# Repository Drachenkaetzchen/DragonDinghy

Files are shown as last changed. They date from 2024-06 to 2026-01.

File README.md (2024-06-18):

DragonDinghy is a small expansion board for Klipper. Your main ship is damaged and lost some of it's functionality? DragonDinghy has you covered. 4 fan Ports (2x GND-switched with tacho, 2x 4-wire fan ports), 4x Neopixel outputs, 9 thermistor inputs, 2x I²C ports, 12V 2A and 5V 2A voltage regulator onboard. Can be operated via USB or CAN

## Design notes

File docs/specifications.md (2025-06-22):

# Specifications

## Main Features

* 9 Thermistor Inputs
    * 5 Inputs best suited for 100k NTCs, like Generic 3950 or ATC Semitec
    * 4 Inputs best suited for PT1000
* 4 Fan Outputs
    * 2 GND-switched PWM fan ports with optional tachometer support, 1 A per port
    * 2 4-pin Fan Ports, 2 A maximum per port
    * Each fan output supports 5V, 12V and 24V fans
* 4 RGB Outputs (compatible with WS2812B, SK6812 and Adafruit Neopixel)
    * Integrated diagnostic SK6812 RGB LED  
    * up to 2A (shared with other 5V devices and across all 4 ports) 
* 2 I²C ports
* Integrated 12V 2A and 5V 2A step-down converters
* Usage via CAN or USB (or...use it as an USB to CAN bridge?)
* Raspberry Pi compatible mounting pattern
* Extensive Quality-of-Life Features
    * All ports are labeled on the board with the pinout and the respective pin for Klipper
    * Klipper `menuconfig` settings are printed on the board
    * Diagnostic LEDs for fan ports, DFU mode and power supply status
* Protection Features
    * Reverse Polarity Protection on the main input
    * Thermistor inputs withstand accidental short to 24V

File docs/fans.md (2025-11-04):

# Fans

This section explains how to figure out what fan you have, and where to connect it.

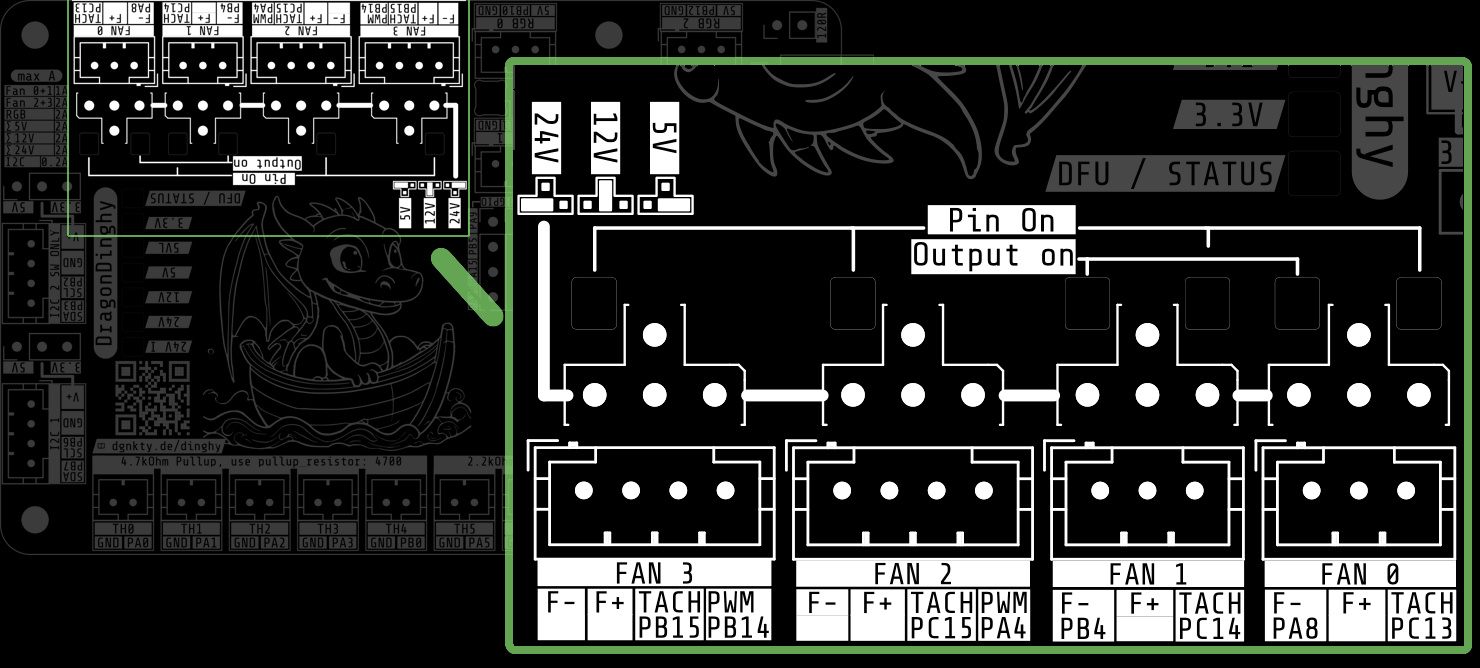
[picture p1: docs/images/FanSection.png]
Fan Section Overview


## Before connecting the fan

Prior connecting, ensure that the fan's maximum current is below the current of 1A (Fan 0/1) or 2A (Fan 2/3).

!!! note

    Please make sure that your fans don't have positive and negative shorted. This can happen easily during installation
    of the toolhead, and happens often behind the fan's label. Therefore, it is good practice to measure continuity
    between the positive and negative fan wires prior powering the printer on.

    While there is some protection of the fan ports, the control element (mosfet) of Fans 0 and 1 can easily blow
    before the protection fuse kicks in.

## Choosing the fan voltage

Use a jumper to select the voltage as indicated below.

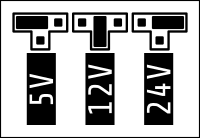
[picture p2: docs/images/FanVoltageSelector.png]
Fan Voltage Jumper


## 2-Wire Fans

Those are the most common type of fans in the 3D printer world. Their speed can only be controlled by rapidly turning
connecting and disconnecting either the positive or negative wire. DragonDinghy, like most other 3D printer boards,
switches these fans on the negative side.

You can connect these fans to the 3 pin fan headers (Fan 0 and Fan 1):

| Wire Color (typical) | Fan 0 | Fan 1 |
|---|---|---|
| Black | F- (PA8) | F- (PB4) |
| Red | F+ | F+ |

The third connector (TACH) is not used in this scenario.

Example Klipper Section:

```
# These are the example configurations for 2-wire fans on Fan 0 and Fan 1
[fan_generic dinghy_fan0]
pin: dinghy:PA8

[fan_generic dinghy_fan1]
pin: dinghy:PB4
```

!!! note 

    Genuine Sunon -A99 series are notoriously hard to control, often they only spin if the speed is set to 100%, and
    turn off or jitter at 99% or below. People have reported success by adjusting Klipper's `cycle_time` parameter,
    but it is by no means guaranteed that these types of fans can be controlled properly.

## 3-Wire Fans

These fans come with a 3rd wire. Most often, the function of those wires is either tachometer or PWM control. You need
to consult your fan's data sheet/seller page to figure out which function that 3rd wire has.

### 3-Wire Fans with Tachometer
For 3-wire fans with tachometers, you can use Fan 0 and Fan 1: 

| Wire Color (typical) | Fan 0 | Fan 1 |
|---|---|---|
| Black | F- (PA8) | F- (PB4) |
| Red | F+ | F+ |
| Blue (Delta), White (Orion), Yellow (GdsTime) | TACH (PC13) | TACH (PC14) |

!!! note

    A diode is already built-in on DragonDinghy, so there is no need to worry about
    the fan spinning or jittering when it's supposed to be off.

Example Klipper Section:

``` { .ini .copy }
# These are the example configurations for Fan 0 and Fan 1
[fan_generic dinghy_fan0]
pin: dinghy:PA8
tachometer_pin: dinghy:PC13

# The following 2 lines are optional, please read the note below
# tachometer_ppr: 2
# tachometer_poll_interval: 0.0009

[fan_generic dinghy_fan1]
pin: dinghy:PB4
tachometer_pin: dinghy:PC14

# The following 2 lines are optional, please read the note below
# tachometer_ppr: 2  
# tachometer_poll_interval: 0.0009
```

!!! note

    `tachometer_ppr` specifies how many impulses per one full fan rotation the fan outputs. That is almost always 2, if
    you have set your `tachometer_poll_interval` correctly, check the fan's datasheet if it uses a different value.

    `tachometer_poll_interval` specifies how often Klipper reads the tachometer pin. The value must be lower than
    `30/(tachometer_ppr*rpm)`. For example, the Delta ASB02505SHA-AY6B requires a poll interval of `0.0009`. Don't use
    arbitarily small values, as this requires additional computational time on the MCUs and can lead to a
    `Timer too close` if improperly configured. 

### 3-Wire Fans with PWM
For 3-wire fans with pwm, you can use Fan 2 and Fan 3. The TACH connector position stays empty in this scenario.

| Wire Color (typical) | Fan 2 | Fan 3 |
|---|---|---|
| Black | F- | F- |
| Red | F+ | F+ |
| Yellow (Delta), Blue (GdsTime, Orion) | PWM (PA4) | PWM (PB14 ) |

Example Klipper Section:

``` { .ini .copy }
# These are the example configurations for Fan 0 and Fan 1
[fan_generic dinghy_fan2]
pin: dinghy:PA4

[fan_generic dinghy_fan3]
pin: dinghy:PB14
```

## 4-Wire Fans

These fans come with 4 wires. Almost always, the additional wires functions for PWM control and tachometer feedback.

These fans go to the Fan 2 and Fan 3 connectors:

| Wire Color (typical) | Fan 2 | Fan 3 |
|---|---|---|
| Black | F- | F- |
| Red | F+ | F+ |
| Blue (Delta), White (Orion), Yellow (GdsTime) | TACH (PC15) | TACH (PB15) |
| Yellow (Delta), Blue (GdsTime, Orion) | PWM (PA4) | PWM (PB14)  |

Example Klipper Section:

``` { .ini .copy }
# These are the example configurations for Fan 0 and Fan 1
[fan_generic dinghy_fan2]
pin: dinghy:PA4
tachometer_pin: dinghy:PC15

# The following 3 lines are optional, please read the note below
# cycle_time: 0.00004
# tachometer_ppr: 2
# tachometer_poll_interval: 0.0009

[fan_generic dinghy_fan3]
pin: dinghy:PB14
tachometer_pin: dinghy:PB15

# The following 3 lines are optional, please read the note below
# cycle_time: 0.00004
# tachometer_ppr: 2  
# tachometer_poll_interval: 0.0009
```

!!! note

    `tachometer_ppr` specifies how many impulses per one full fan rotation the fan outputs. That is almost always 2, if
    you have set your `tachometer_poll_interval` correctly, check the fan's datasheet if it uses a different value.

    `tachometer_poll_interval` specifies how often Klipper reads the tachometer pin. The value must be lower than
    `30/(tachometer_ppr*rpm)`. For example, the Delta ASB02505SHA-AY6B requires a poll interval of `0.0009`. Don't use
    arbitarily small values, as this requires additional computational time on the MCUs and can lead to a
    `Timer too close` if improperly configured.

    `cycle_time` specifies the PWM base frequency. Most PC and server fans expect a 25kHz signal, equalling to
    `cycle_time: 0.00004`

## Troubleshooting

### Fans not spinning

- Ensure that the polarity of the wires is correct.
- Check the voltage status LEDs, they should all be lit

- Check that the `Pin On` LED is lit when you activate the fan.
 
      - If it doesn't light up, you might have the pins set incorrectly. Consult the Klipper log to check that the pins are
        actually set to what you expect them to be set.

#### Fans 0 and 1

- Check that the `Output On` LED is lit when you activate the fan. If it doesn't light up:

      - Ensure the fan voltage jumper is set
      - Ensure the fan is actually connected
      - If the previous checks come back false, then the protection fuse might be blown. This only happens when a severe
        overload happened, for example a short circuit or attempting to run a fan which exceeds the current rating of 1A.
        This fuse is not user replaceable, as other components in that part of the circuit might have taken damage. 

### Fan spinning uncommanded

#### Fans 0 and 1

Check the LEDs of the fan port. If the `Pin On` LED is lit, then something has commanded the fan to spin. This is
typically a misconfiguration or macro on the Klipper side. If `Output On` LED is lit but `Pin On` is not, then the
output has experienced a brief overload (typically a short circuit), fast enough to damage the control element (mosfet)
but not triggering the protection fuse.

#### Fans 2 and 3

Most PWM fans start up at full power until Klipper has started and initialized the MCU board(s). To prevent this,
you can set initial pins in your `make menuconfig` section like so:

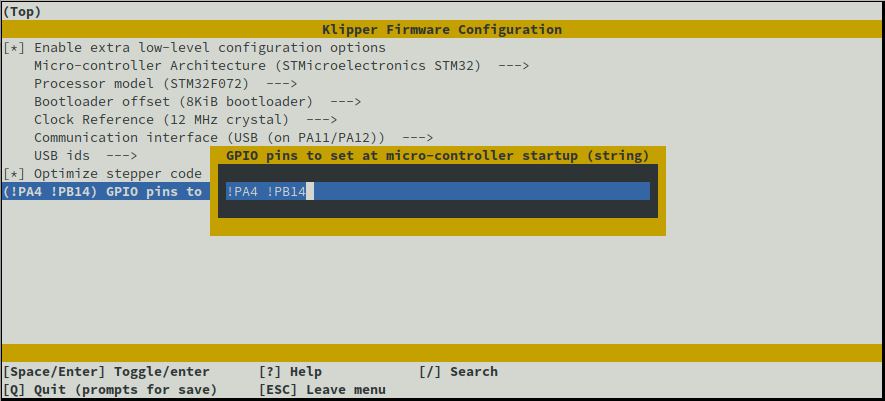
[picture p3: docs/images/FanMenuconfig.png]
Board Diagram


### PWM fans not properly controllable

Many PWM fans designed for use within computers or servers (GdsTime GDP4028, Noctua Fans, almost all PC fans) expact
a 25kHz signal. To implement this, add the following line to your PWM fan section: 

```ini
cycle_time: 0.00004
```

## Appendix
### Typical Fan Wire Colors

This table was written with the most common 3D printer fan models/types in mind. Note that sometimes manufacturers vary
the wire colors by fan model or target audience, so you might want to double-check the fan's data sheet for the most
accurate information.

| Function | Colors |
|---|---|
| Red | Positive supply voltage |
| Black | Negative / GND |
| Tachometer | Blue (Delta), White (Orion), Yellow (GdsTime) |
| PWM Speed Control | Yellow (Delta), Blue (GdsTime, Orion) |
| Alarm | Yellow (Orion) |

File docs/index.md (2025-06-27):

# DragonDinghy

DragonDinghy is a small expansion board for use with [Klipper](https://klipper3d.org).

!!! danger "Work in progress"

    This documentation is a work in progress. Please check back regularly!

    Sadly, it is very warm here, so documentation updates might be delayed. In case of urgent assistance,
    you can always drop an E-Mail to info (at) replimat dot eu with your questions or ask in the #replimat channel
    on the Voron discord.

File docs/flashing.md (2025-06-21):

# Introduction

To make your new board work, you need to put the MCU firmware onto the board. Depending on your scenario, you should use
the excellent guides from Esoterical:

[Esoterical's CAN Bus Guide](https://canbus.esoterical.online/){ .md-button }
[Esoterical's USB Guide](https://usb.esoterical.online/){ .md-button }

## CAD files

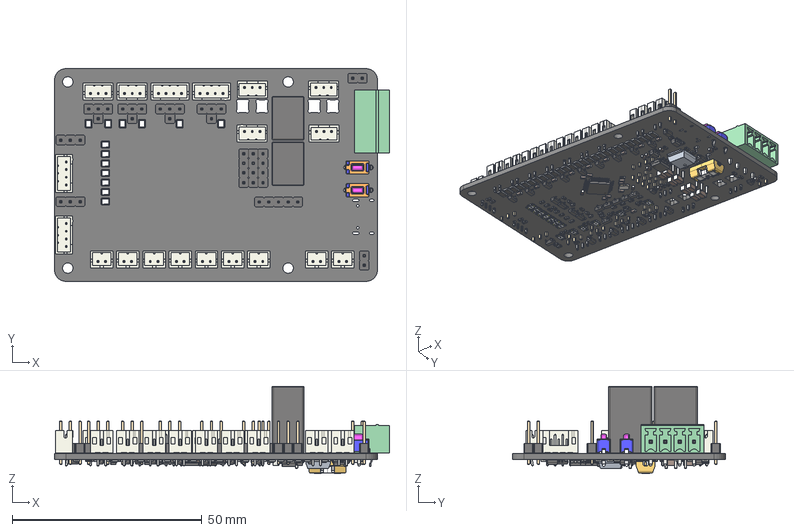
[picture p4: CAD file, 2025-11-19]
STEP/DragonDinghy.step
88.2 x 56.0 x 23.0 mm
SKHLAD x 2
PinHeader_1x05_P2.54mm_Vertical
JST_PH_B4B-PH-K_1x04_P2.00mm_Vertical x 4
JST_PH_B3B-PH-K_1x03_P2.00mm_Vertical x 6
PinHeader_1x03_P2.54mm_Vertical x 6
PinHeader_1x01_P2.54mm_Vertical x 4
JST_PH_B2B-PH-K_1x02_P2.00mm_Vertical x 9
PinHeader_1x04_P2.54mm_Vertical x 3
PinHeader_1x02_P2.54mm_Vertical x 2
PhoenixContact_MC_1,5_4-G-3.81_1x04_P3.81mm_Horizontal
Converter_DCDC_RECOM_R-78B-2.0_THT x 2
R_0603_1608Metric x 45
D_SOD-123 x 6
C_0603_1608Metric x 26
Fuse_0603_1608Metric x 5
R_1206_3216Metric x 27
DragonDinghy 1.49.1
LED-SMD_L3.2-W1.6-RD-EH_WHITE x 13
SOT-23 x 20
C_1206_3216Metric x 8
D_SOD-523 x 4
SOT-23-6
Komponente1
Komponente2
Komponente3
Komponente4
SOIC-8_3.9x4.9mm_P1.27mm
SOT-23-5
SOT-363_SC-70-6 x 3
Crystal_SMD_3225-4Pin_3.2x2.5mm
LQFP-48_7x7mm_P0.5mm
DragonDinghy_PCB

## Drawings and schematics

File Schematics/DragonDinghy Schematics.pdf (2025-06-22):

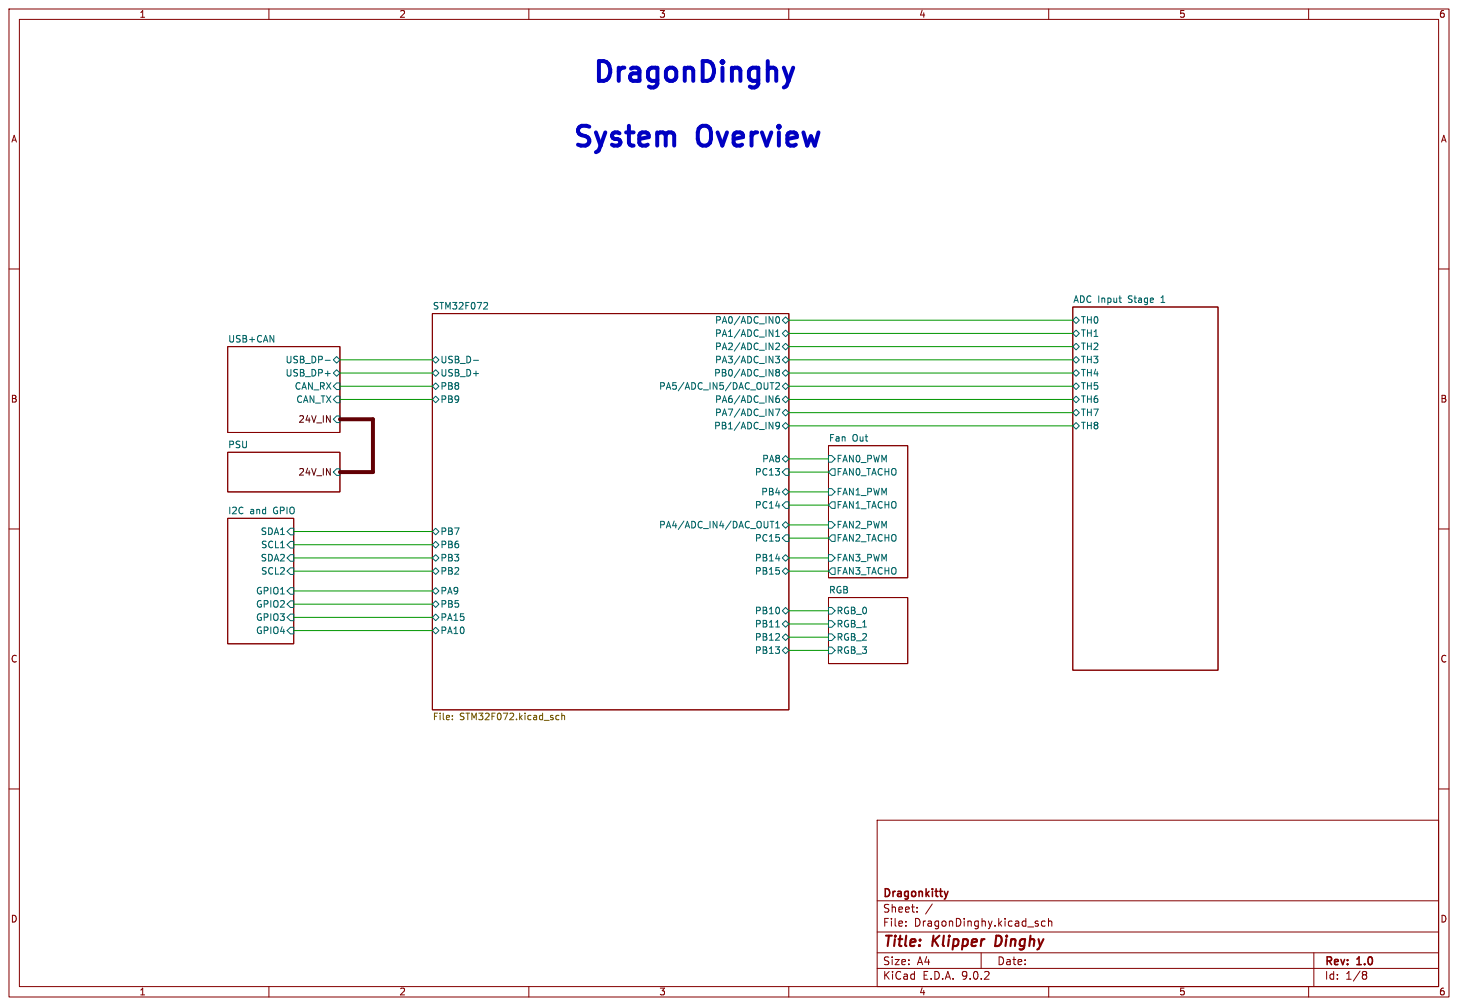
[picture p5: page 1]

File: DragonDinghy.kicad_sch Sheet: / Dragonkitty

Id: 1/8 Title: Klipper Dinghy

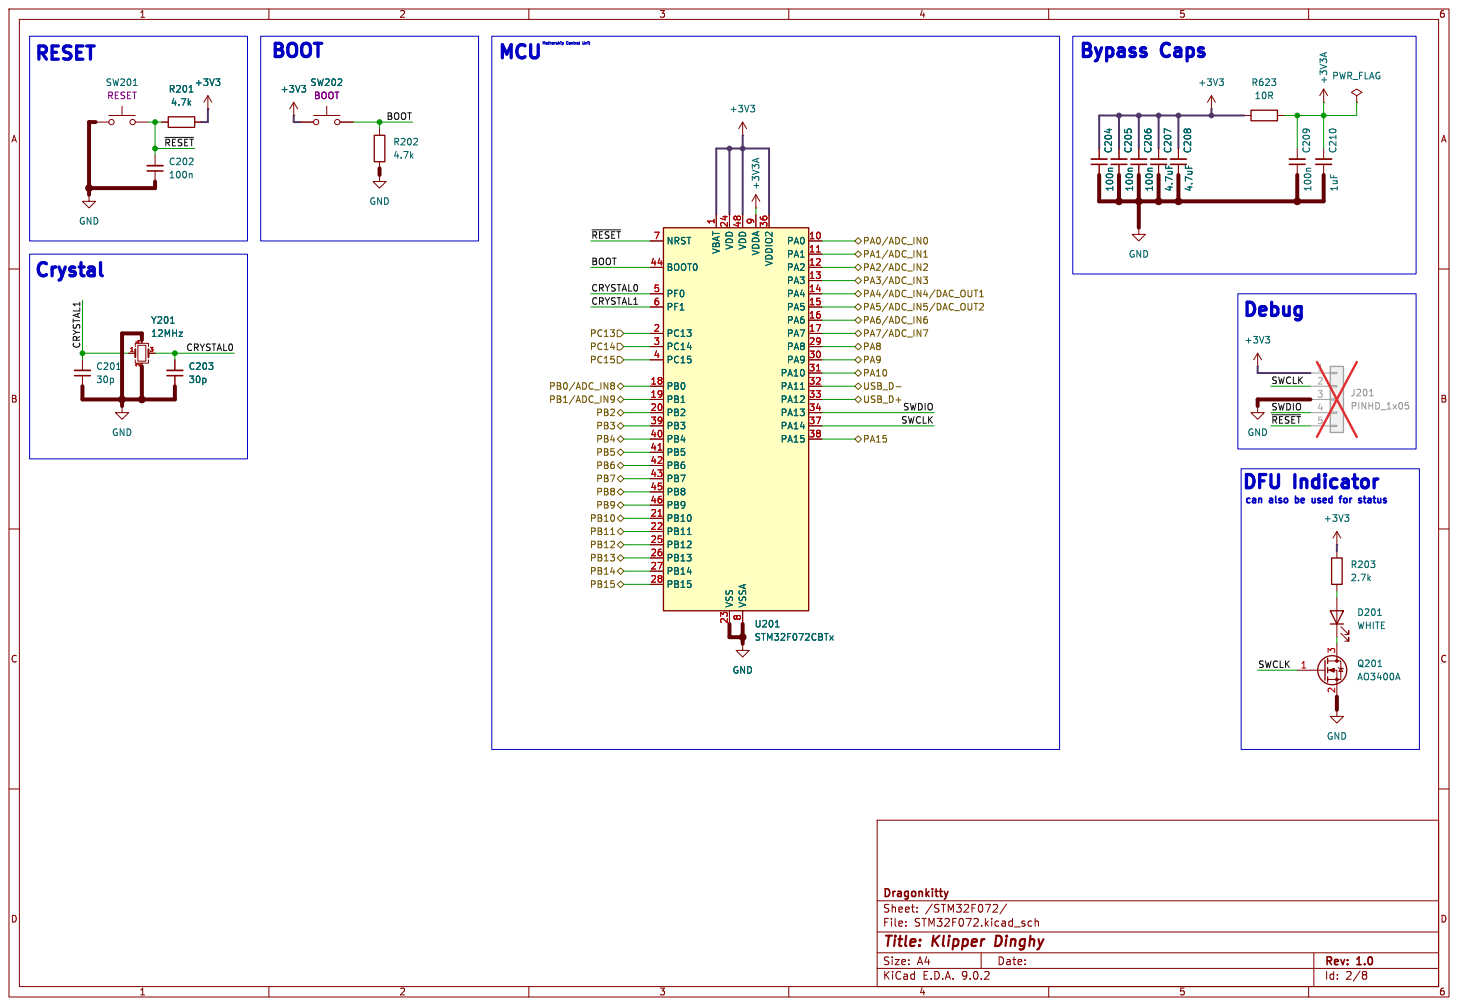
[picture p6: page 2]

can also be used for status RESET

1 VDD 24 VSS 23 VDD 48 VSSA

Id: 2/8 Title: Klipper Dinghy

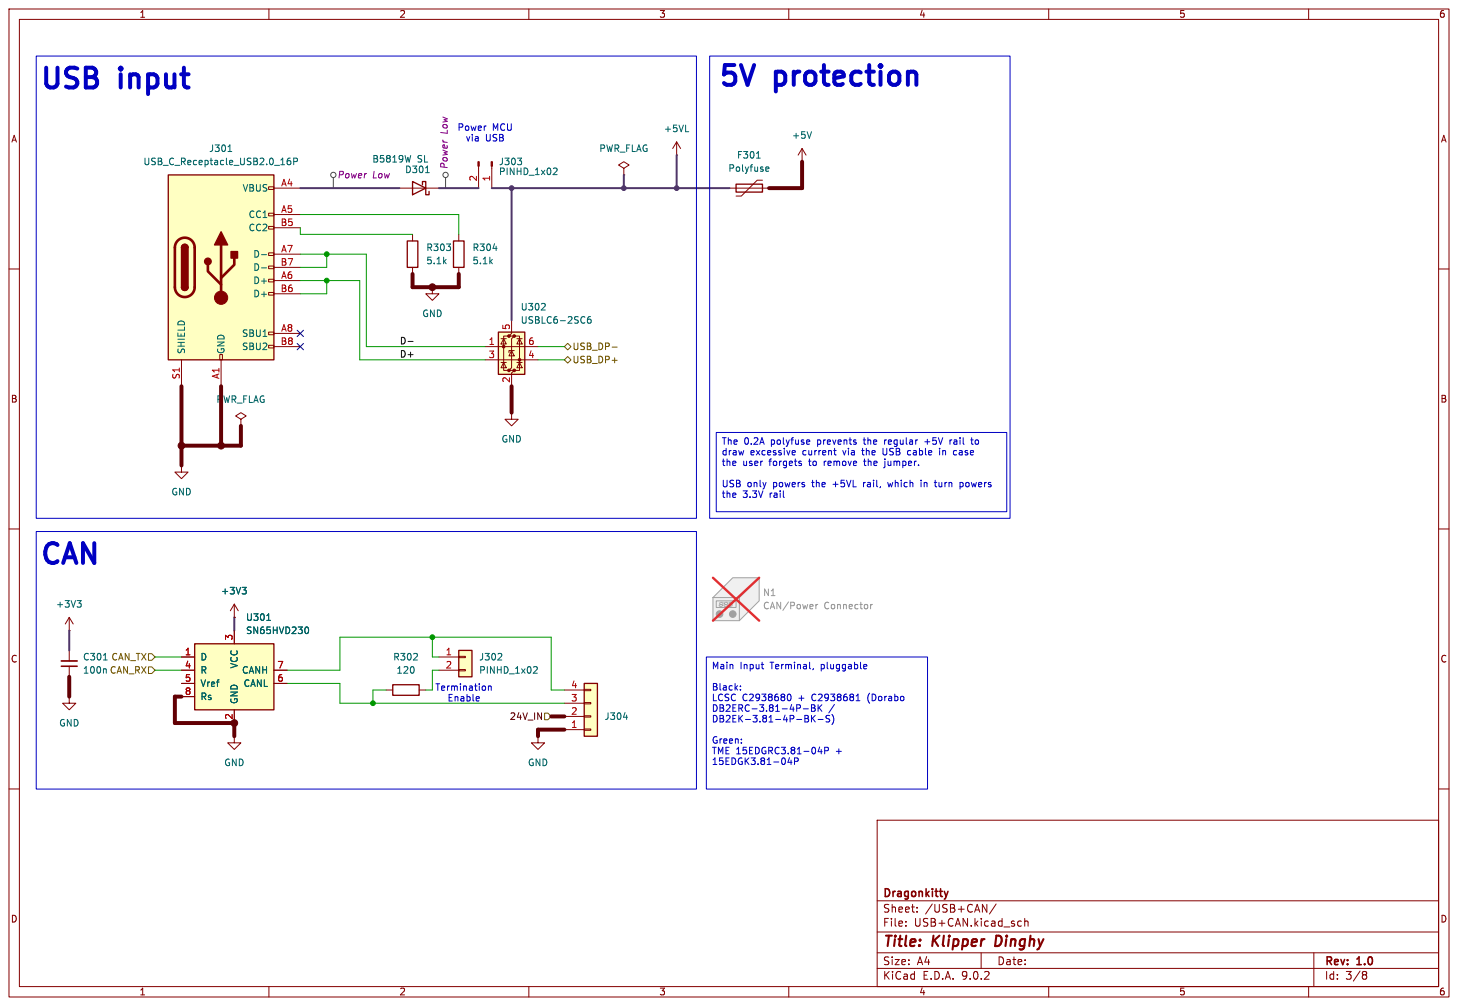
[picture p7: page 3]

draw excessive current via the USB cable in case
the user forgets to remove the jumper. USB only powers the +5VL rail, which in turn powers

File: USB+CAN.kicad_sch Sheet: /USB+CAN/ Dragonkitty GND

Id: 3/8 Title: Klipper Dinghy

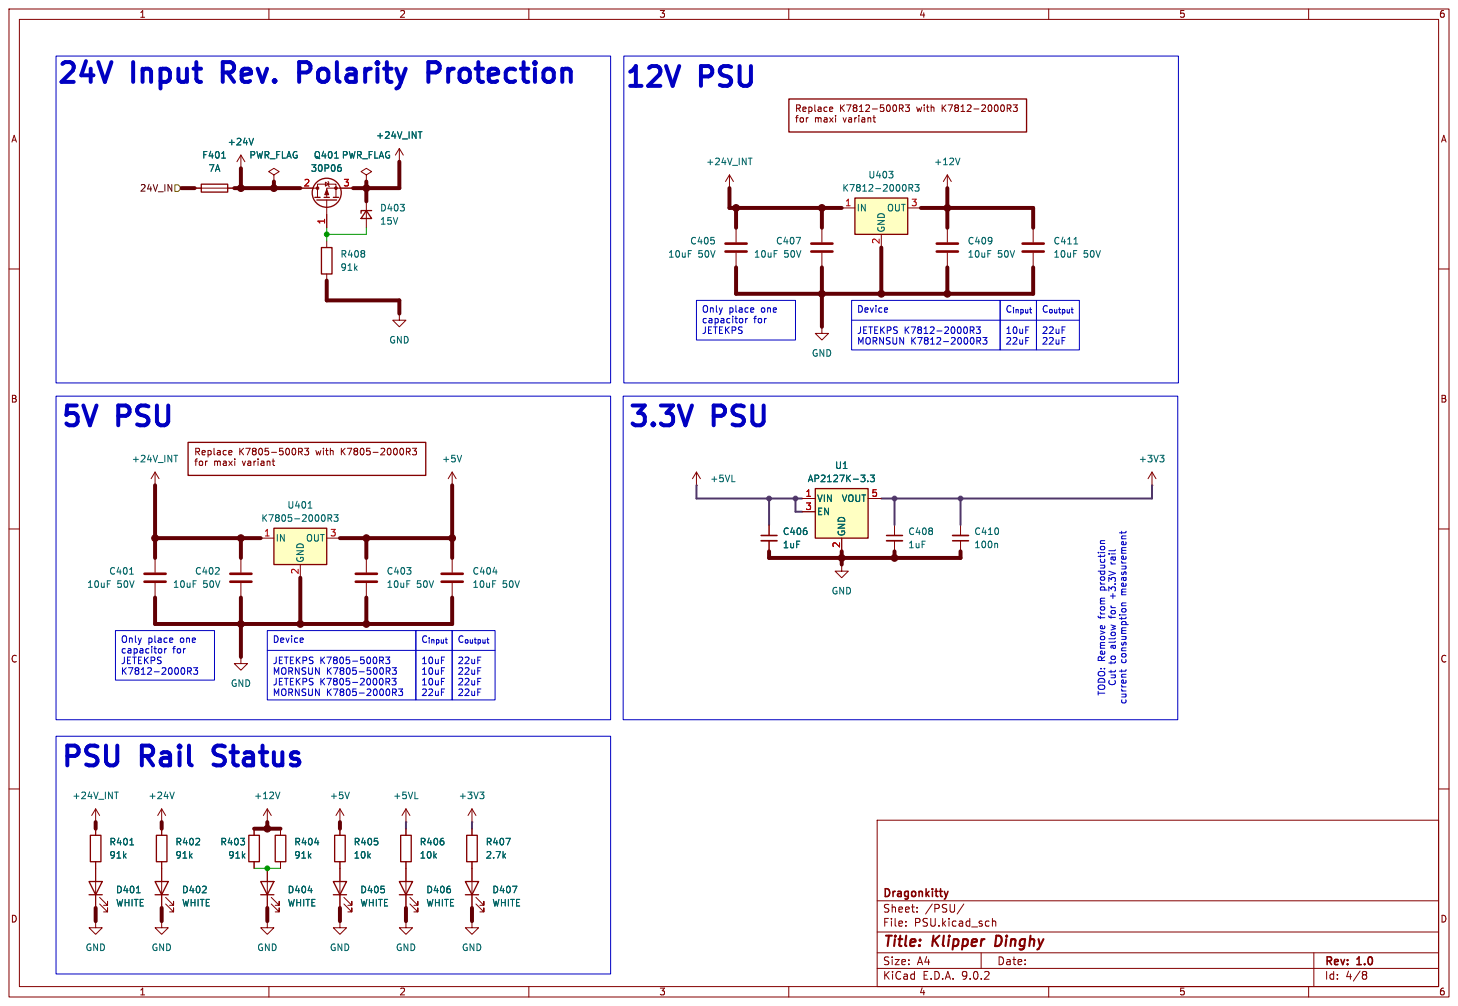
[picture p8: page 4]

24V Input Rev. Polarity Protection

for maxi variant Only place one

+24V_INT C401

Id: 4/8 Title: Klipper Dinghy

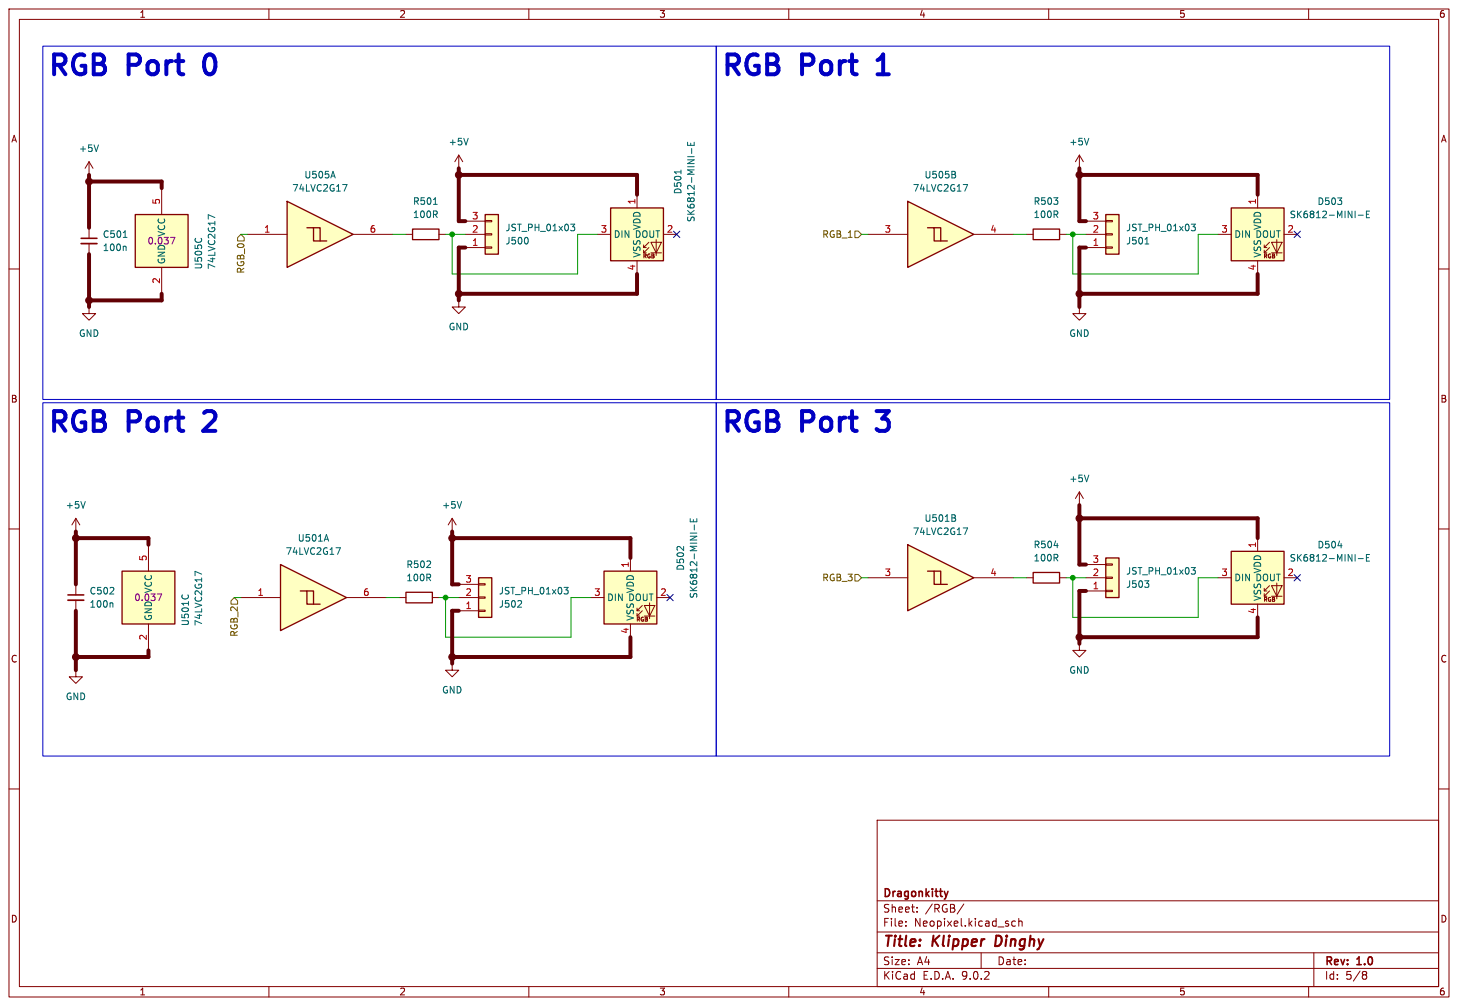
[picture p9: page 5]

2 U501C 74LVC2G17 0.037 RGB_3 RGB_0 RGB_2 RGB_1 RGB Port 2 RGB Port 3

File: Neopixel.kicad_sch Sheet: /RGB/ Dragonkitty

Id: 5/8 Title: Klipper Dinghy

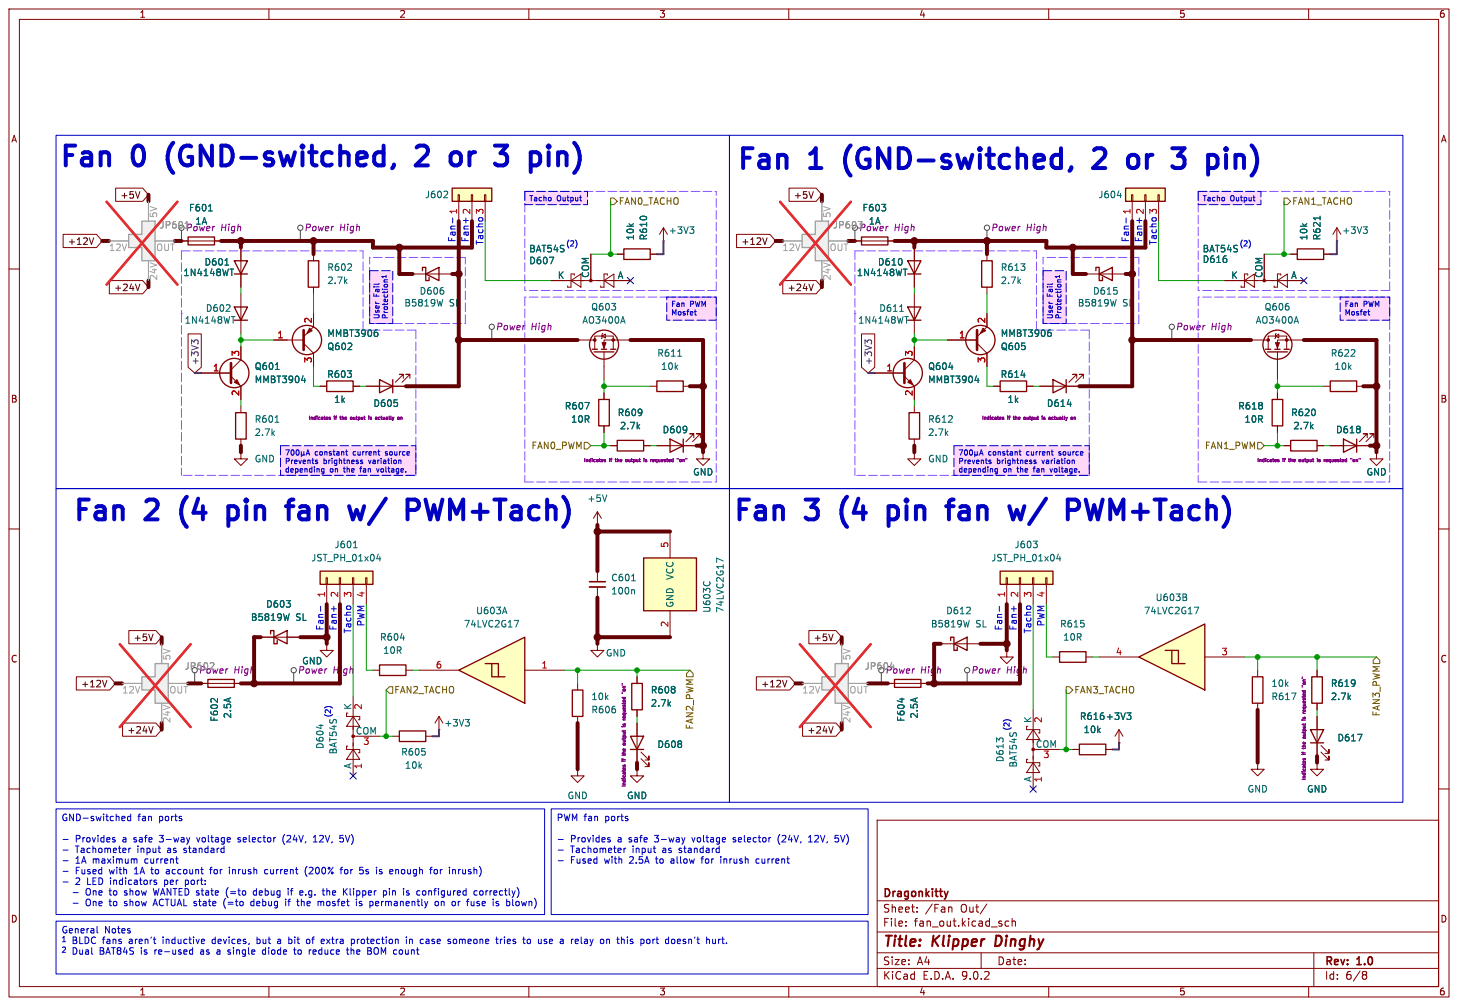
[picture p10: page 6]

Fan 3 (4 pin fan w/ PWM+Tach) Tacho PWMD603 B5819W SLGND F602 2.5A

Fan 2 (4 pin fan w/ PWM+Tach)

2.7k GND
D608 Indicates if the output is requested "on" GND

- Fused with 2.5A to allow for inrush current

File: fan_out.kicad_sch Sheet: /Fan Out/ Dragonkitty

Id: 6/8 Title: Klipper Dinghy

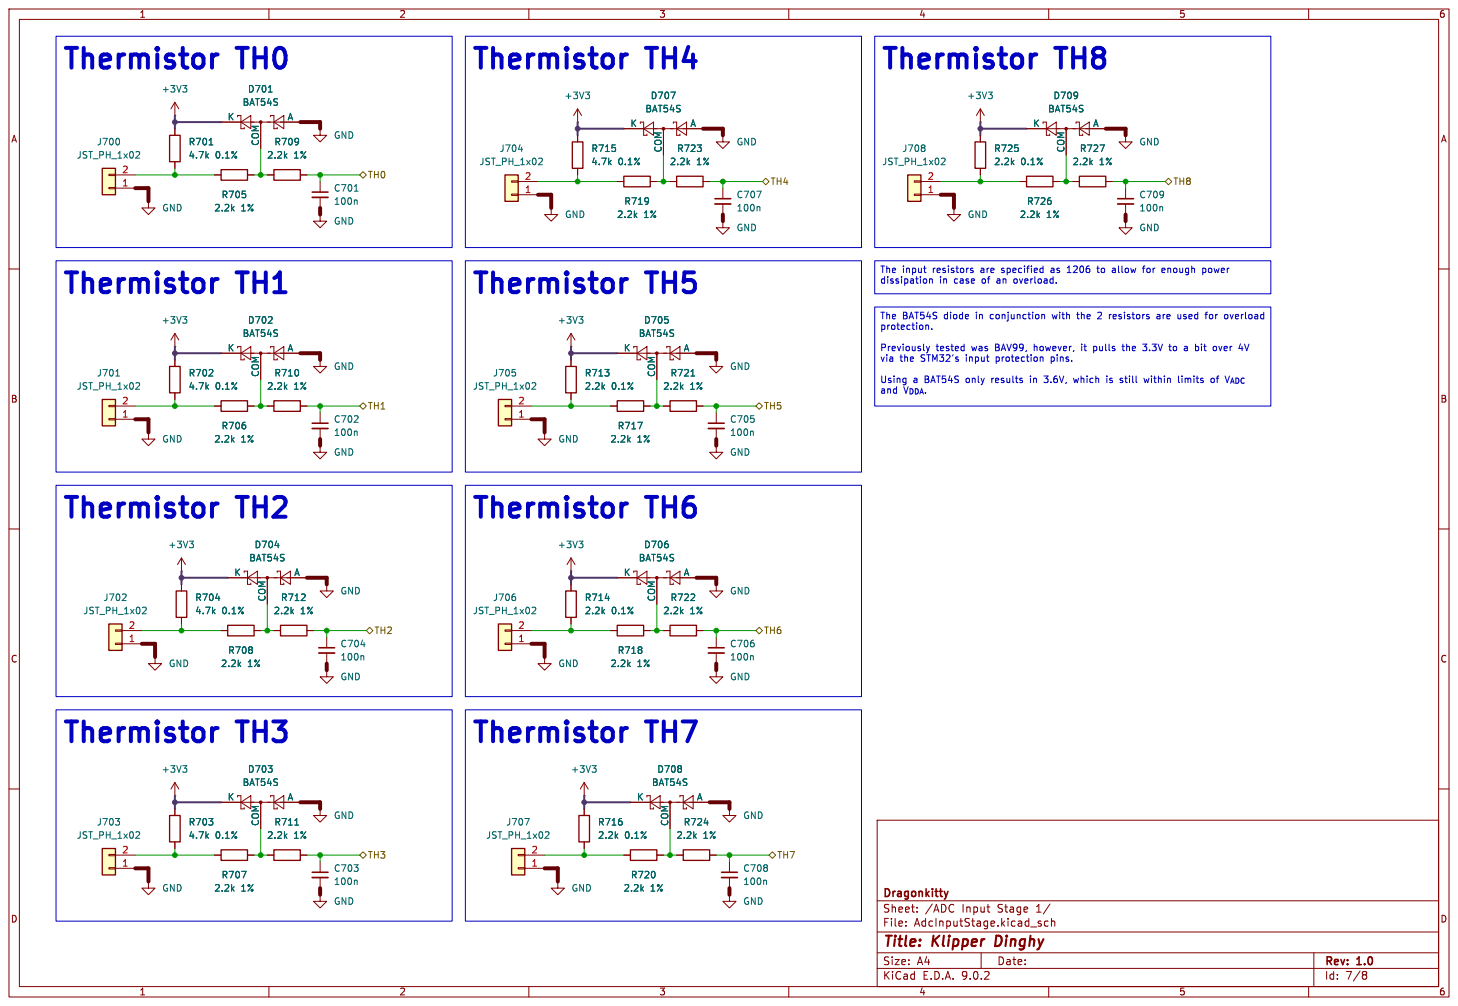
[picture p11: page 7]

Id: 7/8 Title: Klipper Dinghy

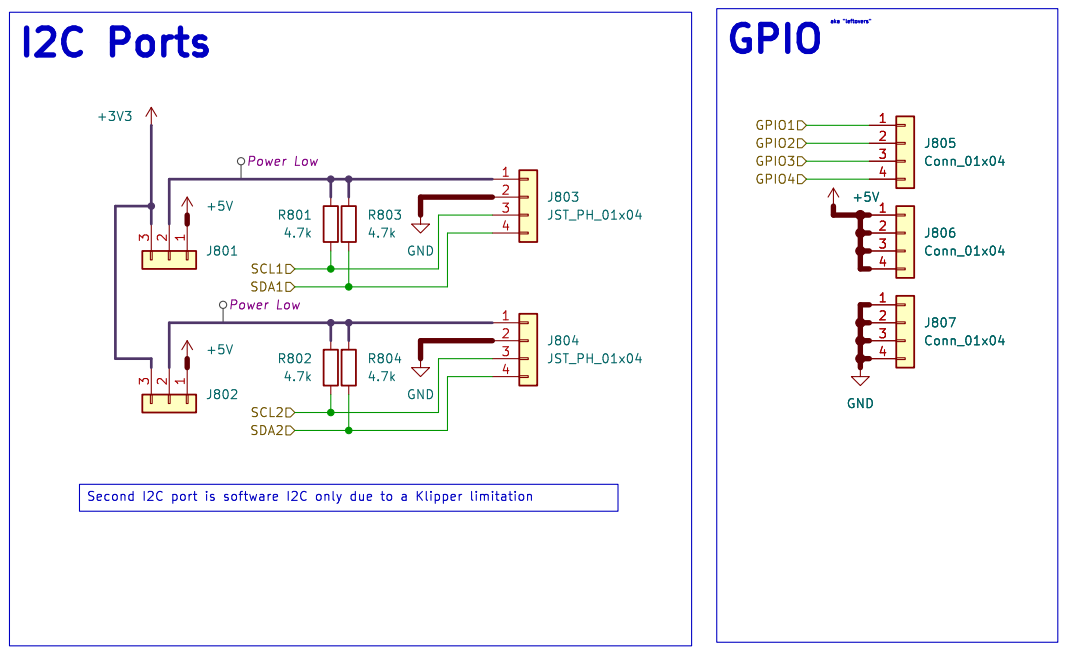
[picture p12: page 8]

Id: 8/8 Title: Klipper Dinghy

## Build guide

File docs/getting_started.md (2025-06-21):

# Getting Started

## Board Overview

<figure class="inline end" markdown="span">
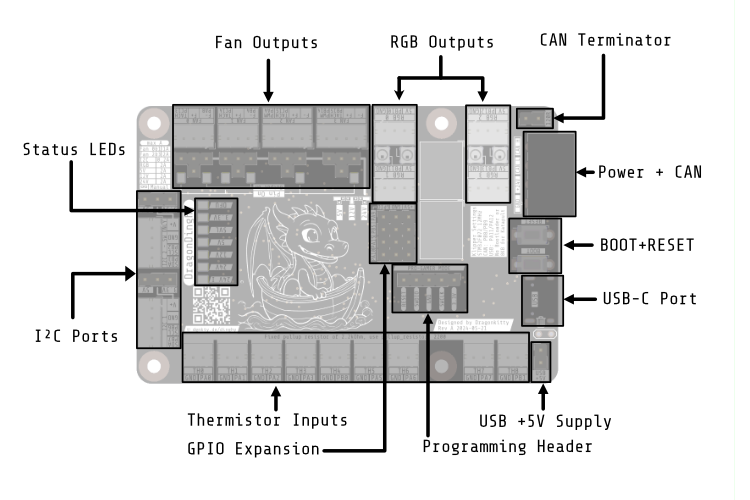
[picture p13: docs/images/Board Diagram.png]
Board Diagram
  
  <figcaption>Board Overview</figcaption>
</figure>

It's a good idea to familiarize yourself with the board layout before continuing. Here's an overview diagram:

## Operation Modes

You can operate the board via USB, CAN or as CAN Bridge, depending on your requirements.

=== "USB"
    The "classic" mode of operation. Requires an USB cable as well as 24V and GND connections. Typical usage scenarios:

    * Board is operated in your electronics bay
    * You don't have a CAN setup

=== "CAN"
    Operation within a CAN network. Requires a CAN interface. Typical usage scenarios:

    * Board is operated outside of your electronics bay
    * You already have a CAN setup

=== "CAN Bridge"
    Operation as a CAN Bridge.  

    * Board is operated inside of your electronics bay
    * You want to save a dedicated CAN interface

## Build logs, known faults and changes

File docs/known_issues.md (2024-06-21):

# Known Issues

## Beta Versions

### Rev A (2024-05-21)

This is the very first revision, shipped to testers only.

#### Issues affecting the users
- Wrong crystal fitted (12MHz instead of 8MHz). Choose 12 MHz in Klipper's `make menuconfig`. 
  A paper label has been placed on the board to document the proper settings.
  
- Reverse polarity protection circuit has been bypassed as reworking would've been too tedious.

- Silkscreen for the RGB headers is flipped 180° (5V is GND and GND is 5V).
  Has been blackened out on the shipped out boards

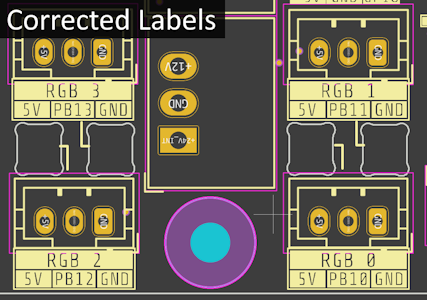
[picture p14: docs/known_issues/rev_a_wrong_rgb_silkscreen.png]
foo
  

#### Issues that need to be reworked
- Wrong footprint for the constant current mirror
- Wrong footprint for the reverse polarity protection P-channel mosfet
- Replace 4 pin input connector with an option for a 6 pin input connector, so that 12V and 5V can be supplied
  externally without the need for the on-board step-down converters - saves a bit of cost and the board can be provided
  in 2 variants, depending on the needs of the user

#### QoL issues
- RGB indicator LEDs are very bright
- RGB indicators should be channel 0,1 and 2,3 instead of 1,0 and 3,2
- Silkscreen hardly readable in several places
- Silkscreen should be rotated in one direction
- RGB debug LED cutouts are not perfectly aligned
- Step-Down Converters are very close to the RGB and extension headers

#### Production Issues
- SMD fuse is very close to through-hole pin headers. Move fuse to make soldering easier
- JST PH Holes are a bit too big, making the connectors fall out
- Step-Down Converter holes are way too big
- Step-Down Converters could be fixated in place by a drop of silicone, but there's little space to do so

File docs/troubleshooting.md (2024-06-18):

# LED Diagnostics

## 5VL and 3.3V lit, 5V off

### Possible Cause
USB 5V Jumper in place and more than 200mA consumption on the 5V rail.

### Explanation
When powering the board via USB (=the 5V USB jumper is in place), you cannot draw more than 200mA from the
5V rail. You should only set the 5V USB jumper if you intend to initially flash the board - once you have flashed
Klipper or Katapult, you should use the respective run-time flashing methods. See [Flashing](flashing.md)

### Solutions

Either perform an [initial flash](flashing.md#initial-flash) or

1. Power off the board
2. Unplug the USB 5V Jumper
3. Perform the [update flash](flashing.md#update-flash)

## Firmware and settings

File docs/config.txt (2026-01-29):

[mcu dinghy]
#serial: 
#canbus_uuid: 

[temperature_sensor f0]
sensor_type: BME280
#i2c_address:
#   Default is 118 (0x76). The BMP180, BMP388 and some BME280 sensors
#   have an address of 119 (0x77).
i2c_mcu: dinghy
i2c_bus: spi1

[temperature_sensor f1]
sensor_type: BME280
i2c_software_scl_pin: dinghy:PB2
i2c_software_sda_pin: dinghy:PB3

[temperature_sensor th0]
sensor_type: Generic 3950
pullup_resistor: 2200
sensor_pin: dinghy:PA0

[temperature_sensor th1]
sensor_type: Generic 3950
pullup_resistor: 2200
sensor_pin: dinghy:PA1

[temperature_sensor th2]
sensor_type: Generic 3950
pullup_resistor: 2200
sensor_pin: dinghy:PA2

[temperature_sensor th3]
sensor_type: Generic 3950
pullup_resistor: 2200
sensor_pin: dinghy:PA3

[temperature_sensor th4]
sensor_type: PT1000
pullup_resistor: 2200
sensor_pin: dinghy:PB0

[temperature_sensor th5]
sensor_type: ATC Semitec 104NT-4-R025H42G
pullup_resistor: 2200
sensor_pin: dinghy:PA5

[temperature_sensor th6]
sensor_type: Generic 3950
pullup_resistor: 2200
sensor_pin: dinghy:PA6

[temperature_sensor th7]
sensor_type: Generic 3950
pullup_resistor: 2200
sensor_pin: dinghy:PA7

[temperature_sensor th8]
sensor_type: Generic 3950
pullup_resistor: 2200
sensor_pin: dinghy:PB1


[neopixel rgb0]
pin: dinghy:PB10
color_order: GRB, GRB, GRB, GRB, GRB, GRB, GRB, GRB, GRBW
chain_count: 9
initial_red: 0.1
initial_green: 0
initial_blue: 0
initial_white: 0.1

[neopixel rgb1]
pin: dinghy:PB11
color_order: GRB, GRB, GRB, GRB, GRB, GRB, GRB, GRB, GRBW
chain_count: 9
initial_red: 0.1
initial_green: 0
initial_blue: 0
initial_white: 0.1

[neopixel rgb2]
pin: dinghy:PB12
color_order: GRB, GRB, GRB, GRB, GRB, GRB, GRB, GRB, GRBW
chain_count: 9
initial_red: 0.1
initial_green: 0
initial_blue: 0
initial_white: 0.1

[neopixel rgb3]
pin: dinghy:PB13
color_order: GRB, GRB, GRB, GRB, GRB, GRB, GRB, GRB, GRBW
chain_count: 9
initial_red: 0.1
initial_green: 0
initial_blue: 0
initial_white: 0.1

[fan_generic fan0]
pin: dinghy:PA8
tachometer_pin: dinghy:PC13

[fan_generic fan1]
pin: dinghy:PB4
tachometer_pin: dinghy:PC14

[fan_generic fan2]
pin: dinghy:PA4
tachometer_pin: dinghy:PC15
tachometer_ppr: 2
tachometer_poll_interval: 0.001
cycle_time: 0.00004
hardware_pwm: true


[fan_generic fan3]
pin: dinghy:PB14
tachometer_pin: dinghy:PB15


    

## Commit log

2025-06-21 Documentation rework
    [config.txt]
2025-06-21 Added schematics
2025-06-22 Updated schematic description and specifications to match reality (Fan 0+1 can support up to 1A each, 500mA was a leftover from the very first revision before I tested it)
2025-06-27 Added fan configuration and troubleshooting section
2025-06-28 Added fan section overview, fixed wrong info in the 3 wire fan PWM section on which connector to skip
2025-11-04 Fixed fan pinout table
2025-11-19 Added STEP
    [DragonDinghy.step]
2026-01-29 Update config.txt
    Added dinghy mcu prefix for all pins
    [config.txt]
